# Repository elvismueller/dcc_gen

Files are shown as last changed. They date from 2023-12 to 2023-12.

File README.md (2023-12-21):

dcc_gen
=======

Simple DCC generator for ATMega8 (V2, schematics and board) and ATMega32 (V3-5, only protoypes) to control small isolated layouts.

Features:
- RS232 Interface (9600 baud) for debugging and simple control (use an normal USB to RS232 converter)
- Heartbeat LED should blink roundabout every 2 sek, fast blinking if waiting for second key
- Connect simple switches (ATMega8 10 inputs | ATMega32 4 groups, 20 Inputs, 80 switches in total)
- Support start-end logic and searches for routes in the internal memory
- Setup for USBProg ISP-Interface adapter by www.embeded-projecs.de (for any other modify platformio.ini)

Toolchain (PlatformIo)
- install Visual Studio Code
- install PlatformIO Extension via Extension Manager (left toolbar). Wait til its installed completely (Icon appears in left toolbar)!
- clone, pull and open workspace dcc_gen
- Build it (bottom bar tick icon)Toolchain
- install driver for USBasp with Zadig (https://zadig.akeo.ie/)
  == USBasp (HK version with fischl.de FW): more or less working with: WinUSB v6.1.7600 and libusb_win32, somehow unreliable
  == USBProg 3 running with modified config (check for platformio.ini)
- use "Upload" in Tasks by click on the PlatformIo Icon (Note: returns an error even if the upload was succesful), check avrdude output!

Toolchain Linux (_Archive)
- sudo aptitude install avr-libc avrdude gcc-avr simulavr
- check/use the Makefile

Kown issues: 
- it is NOT a central unit, just a simple generator
- a lot of hardcoded stuff, no SW to init the memory
- bare metal (no Ardunio Code)
- explizit build for either ATMega8 oder ATMega32
- tested only with a few turnout decoder (Claus Illchmann, LDT Datentechnik) some decoder are not working (QDecoder). 
- like almost all motorshields based on this hardware the generatet DCC signal is not recommended for train control. 
- the ATMega8 is very limited in memory and far less verbose (no help etc.)

Helpers
- read fuses with avrdude: .\avrdude -c avrispmkii -p atmega8 -U lfuse:r:-:i -v
- http://www.engbedded.com/fusecalc
- https://hendrich.org/blogs/mikrocontroller/atmega-644-fuses-setzen/
- programm size: C:/Users/EMM/.platformio/packages/toolchain-atmelavr/bin/avr-size --mcu=atmega8 -C .\firmware.elf

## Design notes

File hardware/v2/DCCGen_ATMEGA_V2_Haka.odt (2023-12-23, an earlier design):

# Bauanleitung SimpleSwitcher 2.0

### Kurzbeschreibung

Die Schaltung erzeugt auf Tastendruck Stellbefehle für DCC Magnetartikel. Damit lassen sich kleine Module mit Standard DCC Komponenten ausrüsten und für mobile Anwendung (Modulanlage bei Austellung) mit einem kleinen Stellpult steuern, gleichzeitig aber auch in größere Anlagen integrieren (Automatische Steuerung zuhause)

Herz der Schaltung ist ein Mikrocontroller der ATMEGA Serie von Atmel. Für die PC Anbindung wird die klassische Schaltung mit dem MAX232 verwendet, Endstufe für die Ausgabe des DCC Signals ist ein L298 damit auch etwas Last auf dem Signal möglich ist.

Über eine PC Oberfläche kann jeder Taste mehrere Magnetartikel zugeordnet werden. Dazu ist eine serielle Schnittstelle (USB-RS232-Adapter falls nicht direkt vorhanden) notwendig.

### Schaltplan:

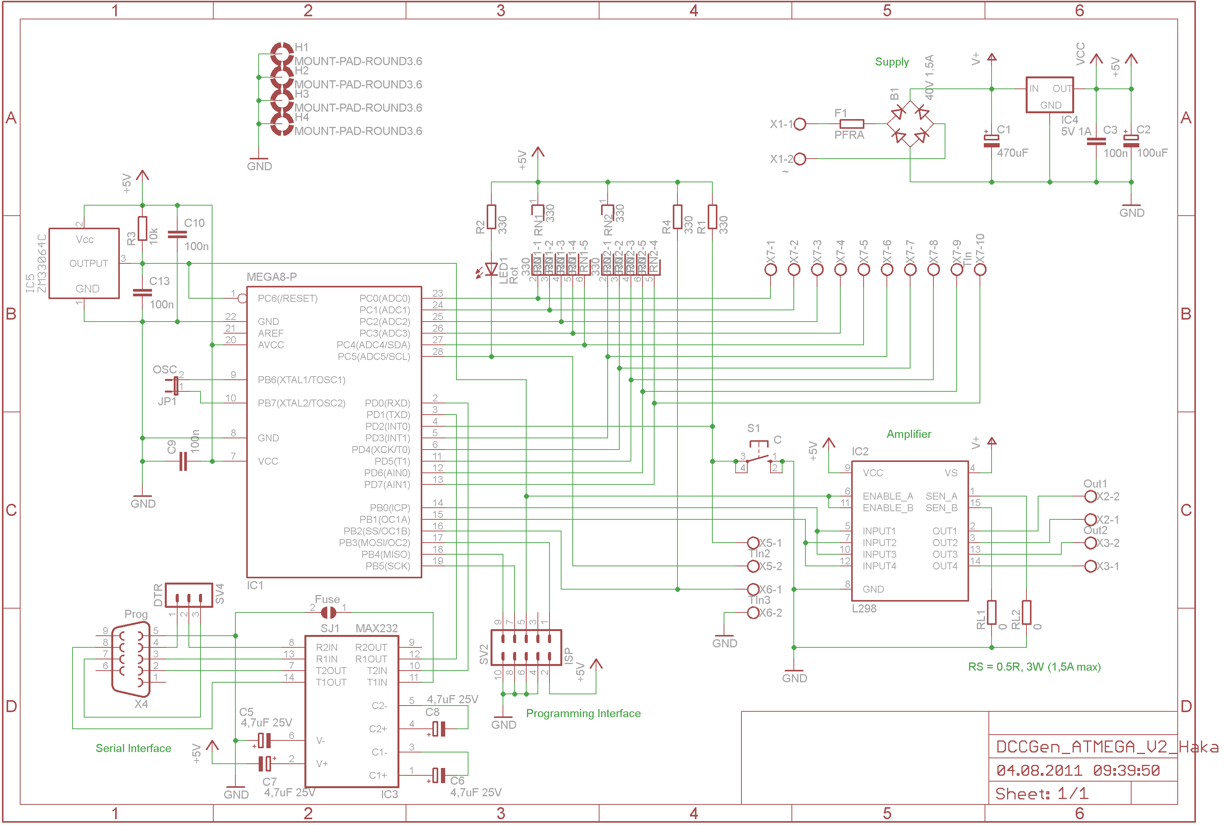
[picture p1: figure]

Beim Aufbau der Schaltung werden die Bauteile der Bauhöhe nach gestaffelt eingebaut. Bei fast allen Bauteilen ist auf die Polung zu achten.

Bei Platinen ohne Bestückungsaufdruck bitte darauf achten das die Bauteile auf die richtige Seite kommen!

Vor dem Einsetzen der IC's das Kapitel Inbetriebnahme lesen!

Viel Glück!

### Bestückungsliste:

Nr. im Plan | Bauteilbeschreibung | Pol? | Reichelt Best.Nr.
R1, R2, R4 | Widerstand 330 Ohm, 1/4W | Nein | 1/4W 330
R3 | Widerstand 10k, 1/4W | Nein | 1/4W 10K
RL1, RL2 | Drahtbrücke | Nein
IC1 | IC-Fassung 28pol | Ja | GS 28-S
IC3 | IC-Fassung 16pol | Ja | GS 16
RN1, RN2 | Widerstandsnetzwerk 6pin, 5x 330 Ohm (andere Werte möglich, nur Pullup) | Ja | SIL 6-5 330
C3, C9, C10, C13 | Keramik Kondensator 100n | Nein | Z5U-2,5 100N
LED1 | LED Rot, 15mA | Ja | LED 3MM RT
IC5 (optional) | Resetcontroller ZM33064C (Ersatz? Ohne?) | Ja | n.a.
B1 | Gleichrichter, 40V, 1.5A | Ja | B40C1500RUND
C5, C6, C7, C8 | Tantal oder Elko, 1uF, min. 25V (siehe Datenblatt!!) | Ja | TANTAL 1,0/35
S1 (optional) | Printtaster, Omron (passt?) | Nein | TASTER 3301
SV2 (optional) | Pfostenleiste, 3pol, einreihig | Nein | SL 1X40G 2,54
SV4 | Pfostenleiste, 10pol, zweireihig | Nein | SL 2X40G 2,54
X1, X2, X3, X5, X6 | Klemmen 2pol | Nein | AKL 057-02
X7 | Klemmen 10pol | Nein | AKL 101-10 oder 5x AKL 057-02
C1 | Elko, 63V, 470uF | Ja | RAD 470/63
C2 | Elko, 35V 100uF | Ja | RAD 10/35
F1 | Halbleitersicherung, 0.5/1A | Nein | PFRA 050
X4 | Sub-D, Print, gewinkelt, 9pol WELCHE??? | Ja | D-SUB BU 09US D-SUB BU 09EU
IC4 | Festspannungsregler 7805 5V, 1A | Ja | µA 7805
IC1 | Mikrocontroller ATMEGA8-P (größere Version??) | Ja | ATMEGA 8-16 DIP (ATMEGA 168-20DIP)
IC2 | L298 | Ja | L 298
IC3 | MAX232 (genauer Typ?) | Ja | MAX 232 CPE

### Korrekturen:

- Am IC MAX232 zusätzlicher Block Kondensator VCC-GND zu Störungsunterdrückung

### Inbetriebnahme

Der Controller arbeitet mit 5V, damit ist die Versorgungsspannung nur durch die gewünschte Digitalspannung definiert. Üblich sind 11-14V~ Wechsel- bzw. 15-20V Gleichspannung. In Verbindung mit Servo-Controller Bausteinen ist es ratsam eher an die untere Grenze zu gehen oder diese komplett separat zu versorgen.

Vor dem Einsetzen der IC's in die Sockel prüfen ob die Versorgungsspannung (Pin 7, Pin 8) am Sockel für den ATMEGA 5V beträgt. Alternativ gemessen über C2.

Dann die IC's einsetzen. Im unprogrammierten Zustand sollte die LED beim Einschalten dreimal blinken und dann erlöschen. Wird ein Eingang betätigt blinkt die LED bis die Fahrstufe abgearbeitet ist.

Zum Testen der Kommunikation mit dem PC die Schaltung an einen freien seriellen Port des PCs anschließen und die Software starten. Die Software sucht automatisch auf allen vorhandenen COM-Ports und verbindet sich mit der Hardware.

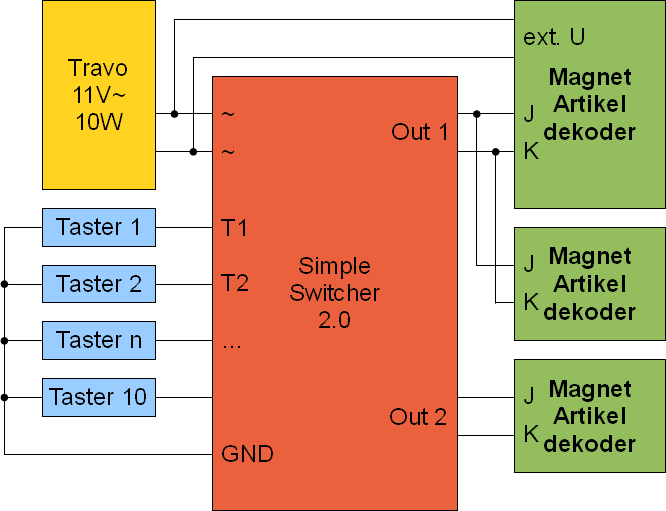
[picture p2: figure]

### Ansicht von der Bestückungsseite

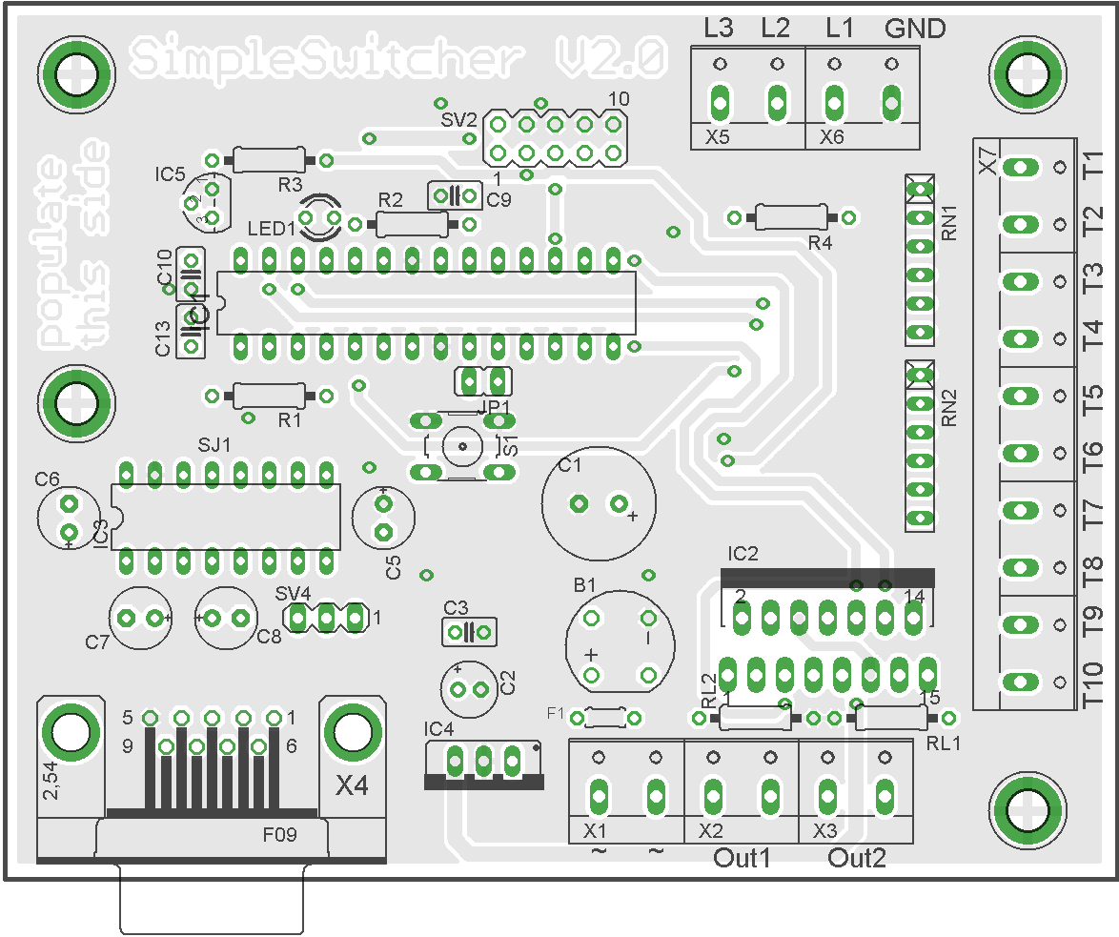
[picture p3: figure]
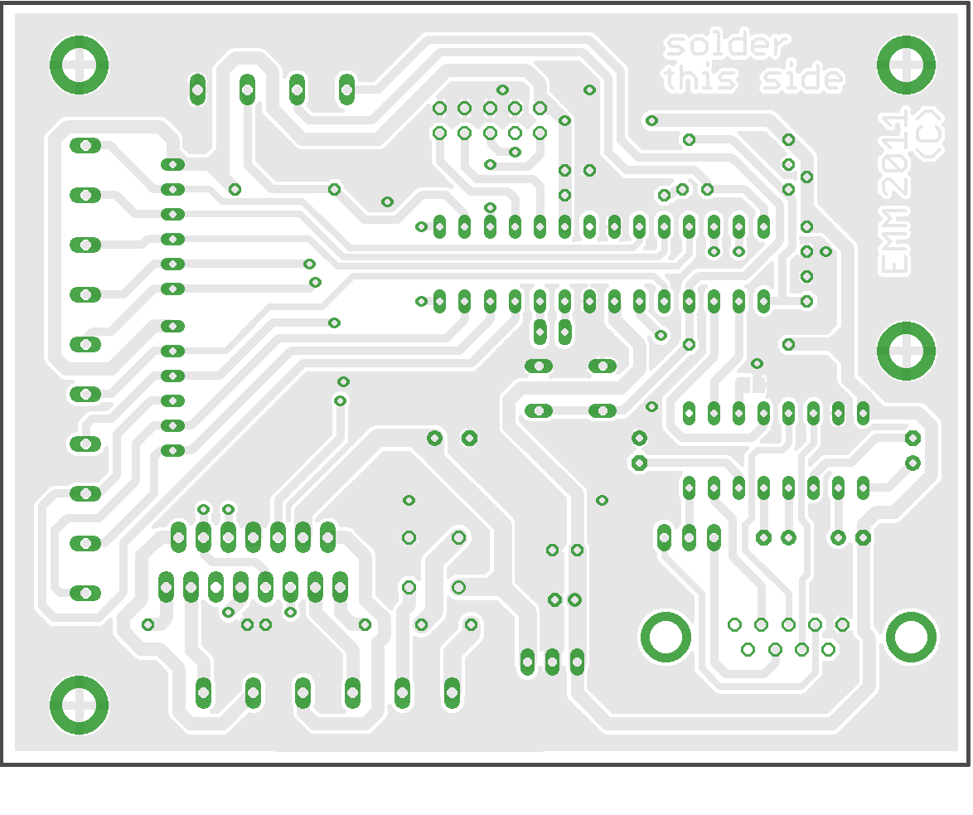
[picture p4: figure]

### Ansicht von der Lötseite

### Kalkulation

Artikel-Nr. | Bezeichnung | WG | Menge | Einzelpreis incl. MwSt. | Gesamtpreis incl. MwSt.
µA 7805 | Spannungsregler 1A positiv, TO-220 | 1 | 1 | 0,29 € | 0,29 €
L 298 | Driver, Multiwatt-15 = L 298N | 1 | 1 | 2,15 € | 2,15 €
ATMEGA 8-16 DIP | ATMega AVR-RISC-Controller, PDIP-28 | 1 | 1 | 2,60 € | 2,60 €
AKL 101-10 | Anschlussklemme 10-polig, RM 5,08 | 1 | 1 | 0,95 € | 0,95 €
AKL 057-02 | Anreihklemme 2-polig, RM5,08 | 1 | 5 | 0,28 € | 1,40 €
1/4W 330 | Kohleschichtwiderstand 1/4W, 5%, 330 Ohm | 1 | 3 | 0,10 € | 0,31 €
1/4W 10K | Kohleschichtwiderstand 1/4W, 5%, 10 K-Ohm | 1 | 1 | 0,10 € | 0,10 €
GS 28-S | IC-Sockel, 28-polig, doppelter Federkontakt | 1 | 1 | 0,080 € | 0,08 €
GS 16 | IC-Sockel, 16-polig, doppelter Federkontakt | 1 | 1 | 0,080 € | 0,08 €
SIL 6-5 330 | Widerstands-Netzwerk, 5Wid./6Pins, 330 Ohm | 1 | 2 | 0,080 € | 0,16 €
Z5U-2,5 100N | Vielschicht-Keramikkondensator 100N, 20% | 1 | 4 | 0,040 € | 0,16 €
LED 3MM RT | LED, 3mm, Low Cost, rot | 1 | 1 | 0,060 € | 0,06 €
B40C1500RUND | RUND-GLEICHRICHTER | 1 | 1 | 0,15 € | 0,15 €
TANTAL 1,0/35 | Tantal-Kondensator, Rm 2,5, 1,0µF/35V | 1 | 4 | 0,14 € | 0,56 €
TASTER 3301 | Kurzhubtaster 6x6mm, Höhe: 4,3mm, 12V, vertikal | 1 | 1 | 0,090 € | 0,09 €
SL 1X40G 2,54 | 40pol. Stiftleiste, gerade, RM 2,54 | 1 | 1 | 0,15 € | 0,15 €
SL 2X40G 2,54 | 2x40pol.-Stiftleiste, gerade, RM 2,54 | 1 | 1 | 0,27 € | 0,27 €
RAD 470/63 | Elektrolytkondensator, 13x25mm, RM 5,0mm | 1 | 1 | 0,14 € | 0,14 €
RAD 10/35 | Elektrolytkondensator, 5x11mm, RM 2,0mm | 1 | 1 | 0,040 € | 0,04 €
PFRA 050 | Rückstellende Sicherungen, max. 40A-60V, 4,0s | 1 | 1 | 0,31 € | 0,31 €
D-SUB BU 09US | D-SUB-Buchse, 9-polig, gewinkelt, RM 7,2 | 1 | 1 | 0,29 € | 0,29 €
MAX 232 CPE | RS232-Driver, DIL-16 | 1 | 1 | 0,41 € | 0,41 €
Warenwert Bauteile | | | | | 10,75 €
Platine | | | | | 20,00 €
Verpackung & Versandkosten | | | | | 5,00 €
Gesamtpreis | | | | | 35,75

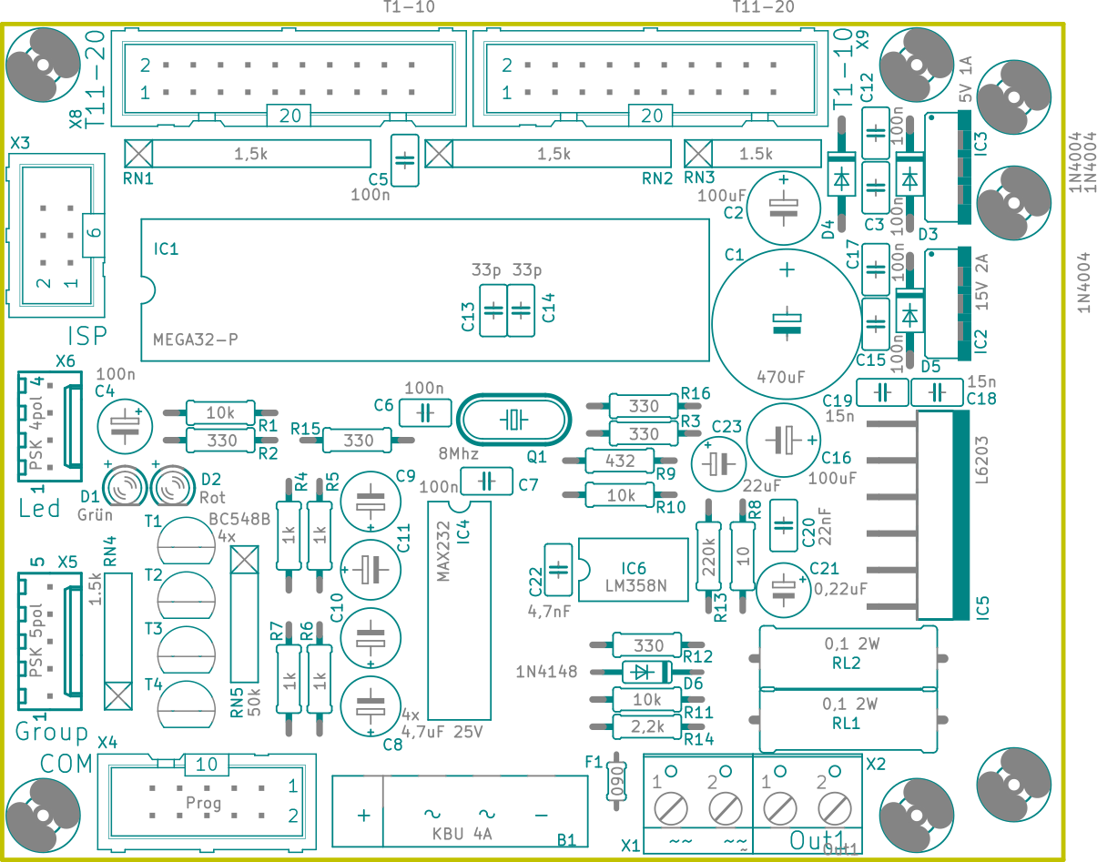
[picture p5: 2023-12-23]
hardware/v5/DCCGen_ATMEGA_V5-brd.png

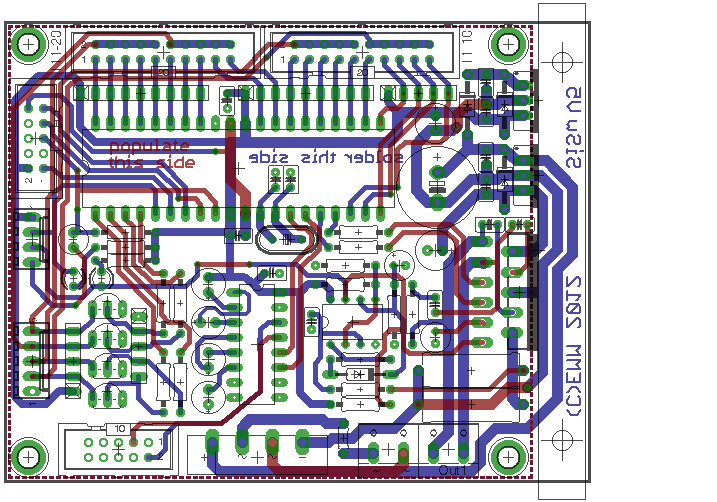
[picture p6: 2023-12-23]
hardware/v5/DCCGen_ATMEGA_V5_Overview.png

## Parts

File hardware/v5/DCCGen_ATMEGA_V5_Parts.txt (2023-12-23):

Partlist

Exported from DCCGen_ATMEGA_V5.sch at 20.07.12 21:43

EAGLE Version 6.2.0 Copyright (c) 1988-2012 CadSoft

Assembly variant: 

Part     Value          Device             Package      Library             Sheet

B1       40V 1.5A       RB1A               RB1A         rectifier           1
C1       470uF          CPOL-EUE5-10.5     E5-10,5      rcl                 1
C2       100uF          CPOL-EUE2-5        E2-5         rcl                 1
C3       100n           C-EU025-025X050    C025-025X050 rcl                 1
C4       100n           CPOL-EUE2.5-5      E2,5-5       rcl                 1
C5       100n           C-EU025-025X050    C025-025X050 rcl                 1
C6       100n           C-EU025-025X050    C025-025X050 rcl                 1
C7       100n           C-EU025-025X050    C025-025X050 rcl                 1
C8       4,7uF 25V      CPOL-EUE2,5-6E     E2,5-6E      rcl                 1
C9       4,7uF 25V      CPOL-EUE2,5-6E     E2,5-6E      rcl                 1
C10      4,7uF 25V      CPOL-EUE2,5-6E     E2,5-6E      rcl                 1
C11      4,7uF 25V      CPOL-EUE2,5-6E     E2,5-6E      rcl                 1
C12      100n           C-EU025-025X050    C025-025X050 rcl                 1
C13      33p            C-EU025-025X050    C025-025X050 rcl                 1
C14      33p            C-EU025-025X050    C025-025X050 rcl                 1
C15      100n           C-EU025-025X050    C025-025X050 rcl                 1
C16      100uF          CPOL-EUE2-5        E2-5         rcl                 1
C17      100n           C-EU025-025X050    C025-025X050 rcl                 1
C18      15n            C-EU025-025X050    C025-025X050 rcl                 1
C19      15n            C-EU025-025X050    C025-025X050 rcl                 1
C20      22nF           C-EU025-025X050    C025-025X050 rcl                 1
C21      0,22uF         CPOL-EUE2-5        E2-5         rcl                 1
C22      4,7nF          C-EU025-025X050    C025-025X050 rcl                 1
C23      22uF           CPOL-EUE2-5        E2-5         rcl                 1
D1       Rot            LED3MM             LED3MM       led                 1
D2       1N4004         1N4004             DO41-10      diode               1
D3       1N4004         1N4004             DO41-10      diode               1
D4       1N4004         1N4004             DO41-10      diode               1
D5       1N4148         1N4148DO35-10      DO35-10      diode               1
D6       Rot            LED3MM             LED3MM       led                 1
F1       PFRA           R-EU_0204/5        0204/5       rcl                 1
H1       3.6            MOUNT-PAD-ROUND3.6 3,6-PAD      holes               1
H2       3.6            MOUNT-PAD-ROUND3.6 3,6-PAD      holes               1
H3       3.6            MOUNT-PAD-ROUND3.6 3,6-PAD      holes               1
H4       3.6            MOUNT-PAD-ROUND3.6 3,6-PAD      holes               1
IC1      MEGA32-P       MEGA32-P           DIL40        atmel               1
IC2      15V 2A         78XXS              78XXS        v-reg               1
IC3      MAX232         MAX232             DIL16        maxim               1
IC4      5V 1A          78XXS              78XXS        v-reg               1
IC5      L6203          L6203              MULTIWATT-11 st-microelectronics 1
IC6      LM358N         LM358N             DIL08        linear              1
Q1       8Mhz           CRYSTALHC49U-V     HC49U-V      crystal             1
R1       10k            R-EU_0207/10       0207/10      rcl                 1
R2       330            R-EU_0207/10       0207/10      rcl                 1
R3       330            R-EU_0207/10       0207/10      rcl                 1
R4       1k             R-EU_0207/10       0207/10      rcl                 1
R5       1k             R-EU_0207/10       0207/10      rcl                 1
R6       1k             R-EU_0207/10       0207/10      rcl                 1
R7       1k             R-EU_0207/10       0207/10      rcl                 1
R8       10             R-EU_0207/10       0207/10      rcl                 1
R9       432            R-EU_0207/10       0207/10      rcl                 1
R10      10k            R-EU_0207/10       0207/10      rcl                 1
R11      10k            R-EU_0207/10       0207/10      rcl                 1
R12      330            R-EU_0207/10       0207/10      rcl                 1
R13      220k           R-EU_0207/10       0207/10      rcl                 1
R16      2,2k           R-EU_0207/10       0207/10      rcl                 1
R17      330            R-EU_0207/10       0207/10      rcl                 1
RL1      0,1 2W         R-EU_0411/15       0411/15      rcl                 1
RL2      0,1 2W         R-EU_0411/15       0411/15      rcl                 1
RN1      1,5k           RNX8               RN-9         resistor-net        1
RN2      1,5k           RNX8               RN-9         resistor-net        1
RN3      1.5k           RNX4               RN-5         resistor-net        1
RN4      1.5k           RNX4               RN-5         resistor-net        1
RN5      50k            RNX4               RN-5         resistor-net        1
SJ1      Fuse           SJ                 SJ           jumper              1
SJ2      Fuse           SJ                 SJ           jumper              1
SJ7      0              SJ                 SJ           jumper              1
T1       BC548B         BC548B             TO92-EBC     transistor-npn      1
T2       BC548B         BC548B             TO92-EBC     transistor-npn      1
T3       BC548B         BC548B             TO92-EBC     transistor-npn      1
T4       BC548B         BC548B             TO92-EBC     transistor-npn      1
X1       ~              W237-02P           W237-132     con-wago-508        1
X2       Out1           W237-02P           W237-132     con-wago-508        1
X4       Prog           F09VP              F09VP        con-subd            1
X5       group          W237-05P           W237-5P      con-wago-508        1
X6       ISP            ML10               ML10         con-ml              1
X7       led            W237-02P           W237-132     con-wago-508        1
X8       T1-10          ML20               ML20         con-ml              1
X9       T11-20         ML20               ML20         con-ml              1

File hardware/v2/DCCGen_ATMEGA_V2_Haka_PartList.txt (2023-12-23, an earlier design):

Partlist

Exported from DCCGen_ATMEGA_V2_Haka.sch at 05.08.2011 10:19:21

EAGLE Version 5.11.0 Copyright (c) 1988-2010 CadSoft

Part     Value              Device             Package      Library             Sheet

B1       40V 1.5A           RB1A               RB1A         rectifier           1
C1       470uF              CPOL-EUE3.5-10     E3,5-10      rcl                 1
C2       100uF              CPOL-EUE2-5        E2-5         rcl                 1
C3       100n               C-EU025-025X050    C025-025X050 rcl                 1
C5       4,7uF 25V          CPOL-EUE2,5-6E     E2,5-6E      rcl                 1
C6       4,7uF 25V          CPOL-EUE2,5-6E     E2,5-6E      rcl                 1
C7       4,7uF 25V          CPOL-EUE2,5-6E     E2,5-6E      rcl                 1
C8       4,7uF 25V          CPOL-EUE2,5-6E     E2,5-6E      rcl                 1
C9       100n               C-EU025-025X050    C025-025X050 rcl                 1
C10      100n               C-EU025-025X050    C025-025X050 rcl                 1
C13      100n               C-EU025-025X050    C025-025X050 rcl                 1
F1       PFRA               R-EU_0204/5        0204/5       rcl                 1
H1       MOUNT-PAD-ROUND3.6 MOUNT-PAD-ROUND3.6 3,6-PAD      holes               1
H2       MOUNT-PAD-ROUND3.6 MOUNT-PAD-ROUND3.6 3,6-PAD      holes               1
H3       MOUNT-PAD-ROUND3.6 MOUNT-PAD-ROUND3.6 3,6-PAD      holes               1
H4       MOUNT-PAD-ROUND3.6 MOUNT-PAD-ROUND3.6 3,6-PAD      holes               1
IC1      MEGA8-P            MEGA8-P            DIL28-3      atmel               1
IC2      L298               L298               MULTIWATT-15 st-microelectronics 1
IC3      MAX232             MAX232             DIL16        maxim               1
IC4      5V 1A              78XXS              78XXS        v-reg               1
IC5      ZM33064C           ZM33064C           TO92         andereBauteile      1
JP1      OSC                JP1E               JP1          jumper              1
LED1     Rot                LED3MM             LED3MM       led                 1
R1       330                R-EU_0207/10       0207/10      rcl                 1
R2       330                R-EU_0207/10       0207/10      rcl                 1
R3       10k                R-EU_0207/10       0207/10      rcl                 1
R4       330                R-EU_0207/10       0207/10      rcl                 1
RL1      0                  R-EU_0207/10       0207/10      rcl                 1
RL2      0                  R-EU_0207/10       0207/10      rcl                 1
RN1      330                RNX5               RN-6         resistor-net        1
RN2      330                RNX5               RN-6         resistor-net        1
S1       C                  10-XX              B3F-10XX     switch-omron        1
SJ1      Fuse               SJ                 SJ           jumper              1
SV2      ISP                MA05-2             MA05-2       con-lstb            1
SV4      DTR                MA03-1             MA03-1       con-lstb            1
X1       ~                  W237-02P           W237-132     con-wago-508        1
X2       Out1               W237-02P           W237-132     con-wago-508        1
X3       Out2               W237-02P           W237-132     con-wago-508        1
X4       Prog               F09HP              F09HP        con-subd            1
X5       TIn2               W237-02P           W237-132     con-wago-508        1
X6       TIn3               W237-02P           W237-132     con-wago-508        1
X7       TIn                W237-10P           W237-10P     con-wago-508        1

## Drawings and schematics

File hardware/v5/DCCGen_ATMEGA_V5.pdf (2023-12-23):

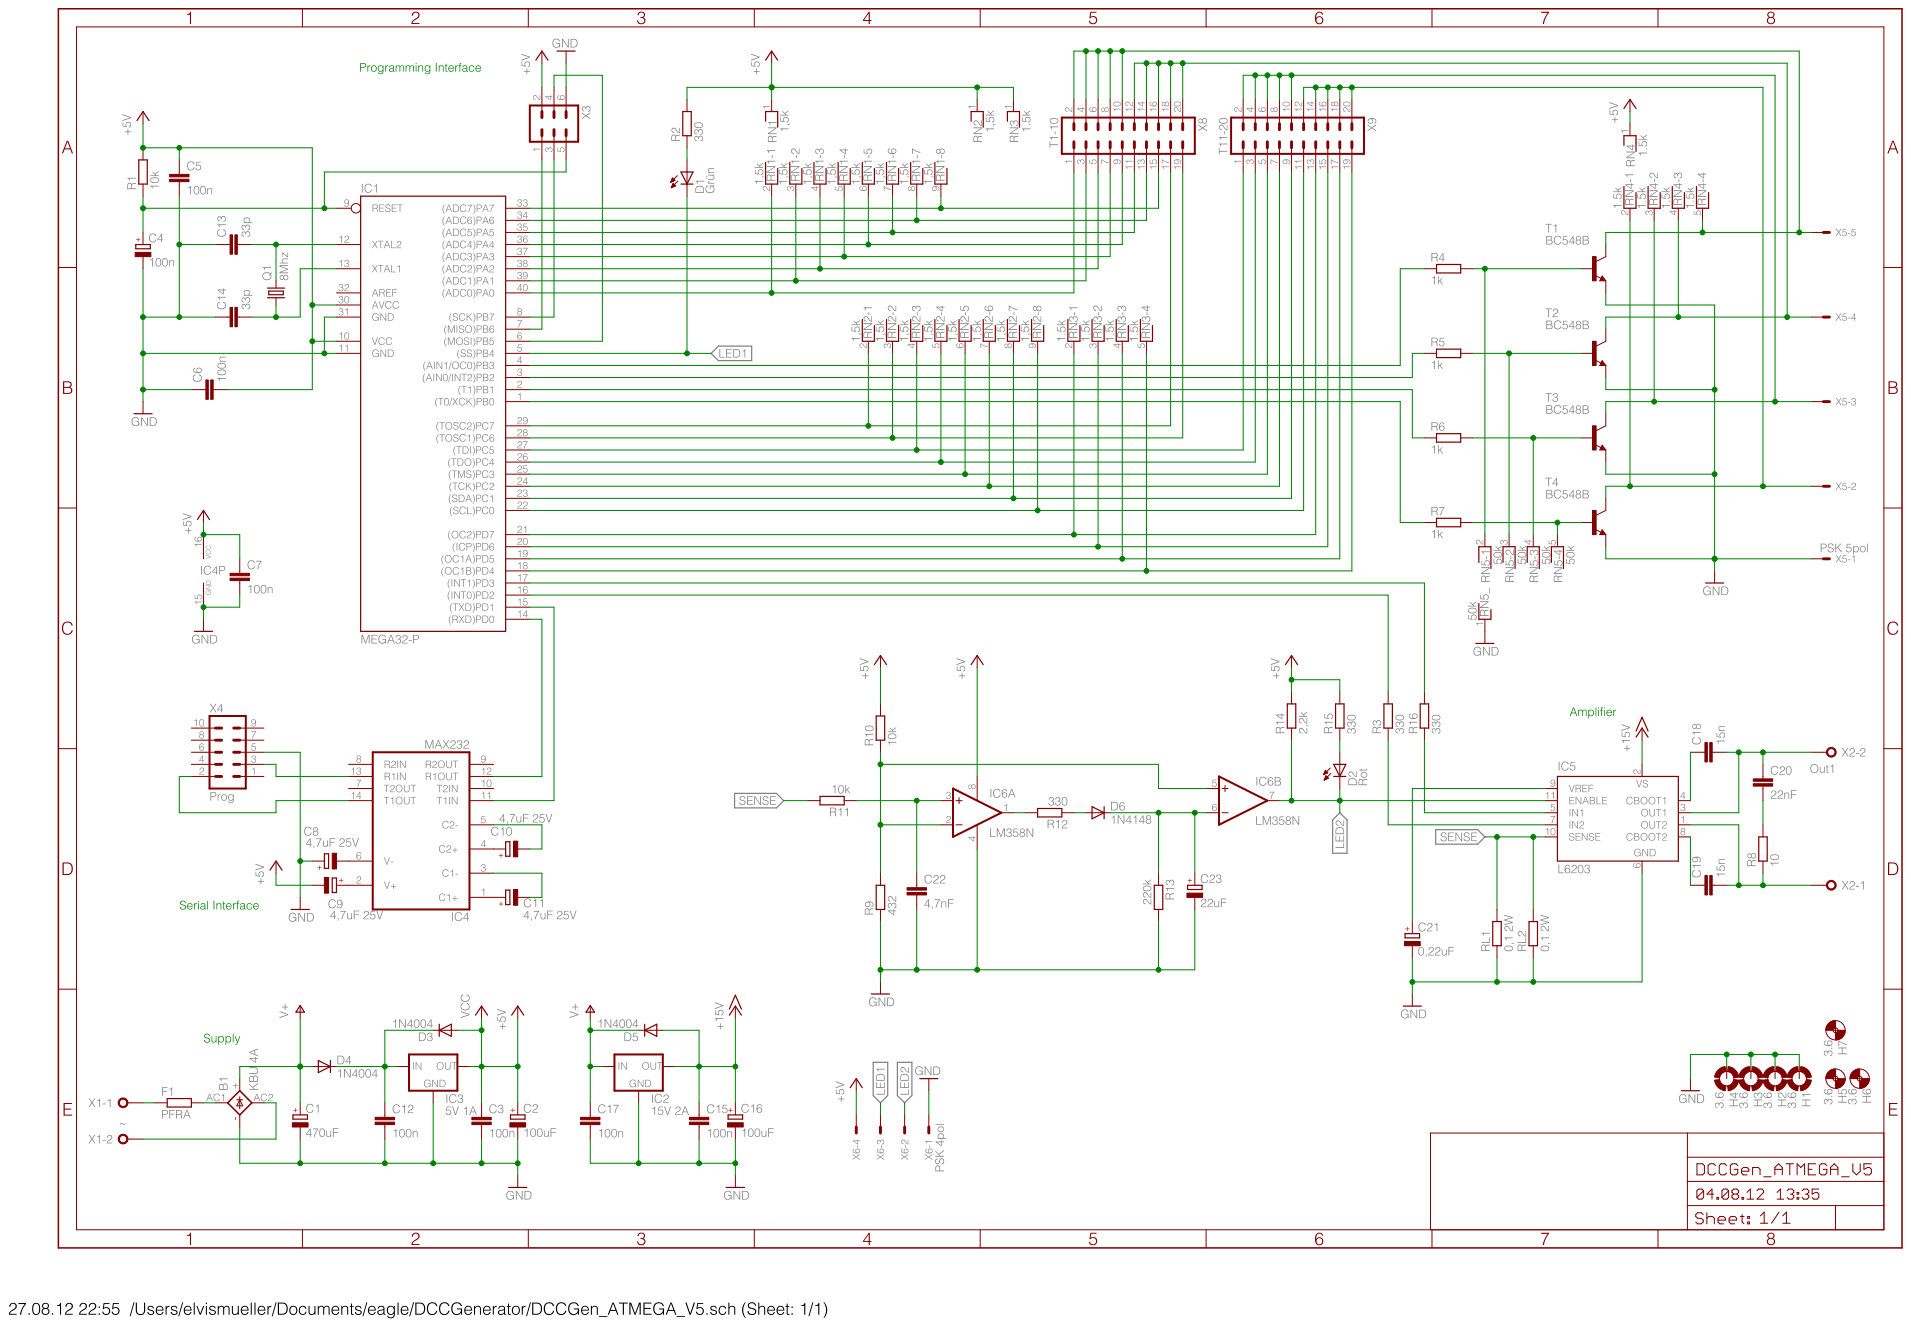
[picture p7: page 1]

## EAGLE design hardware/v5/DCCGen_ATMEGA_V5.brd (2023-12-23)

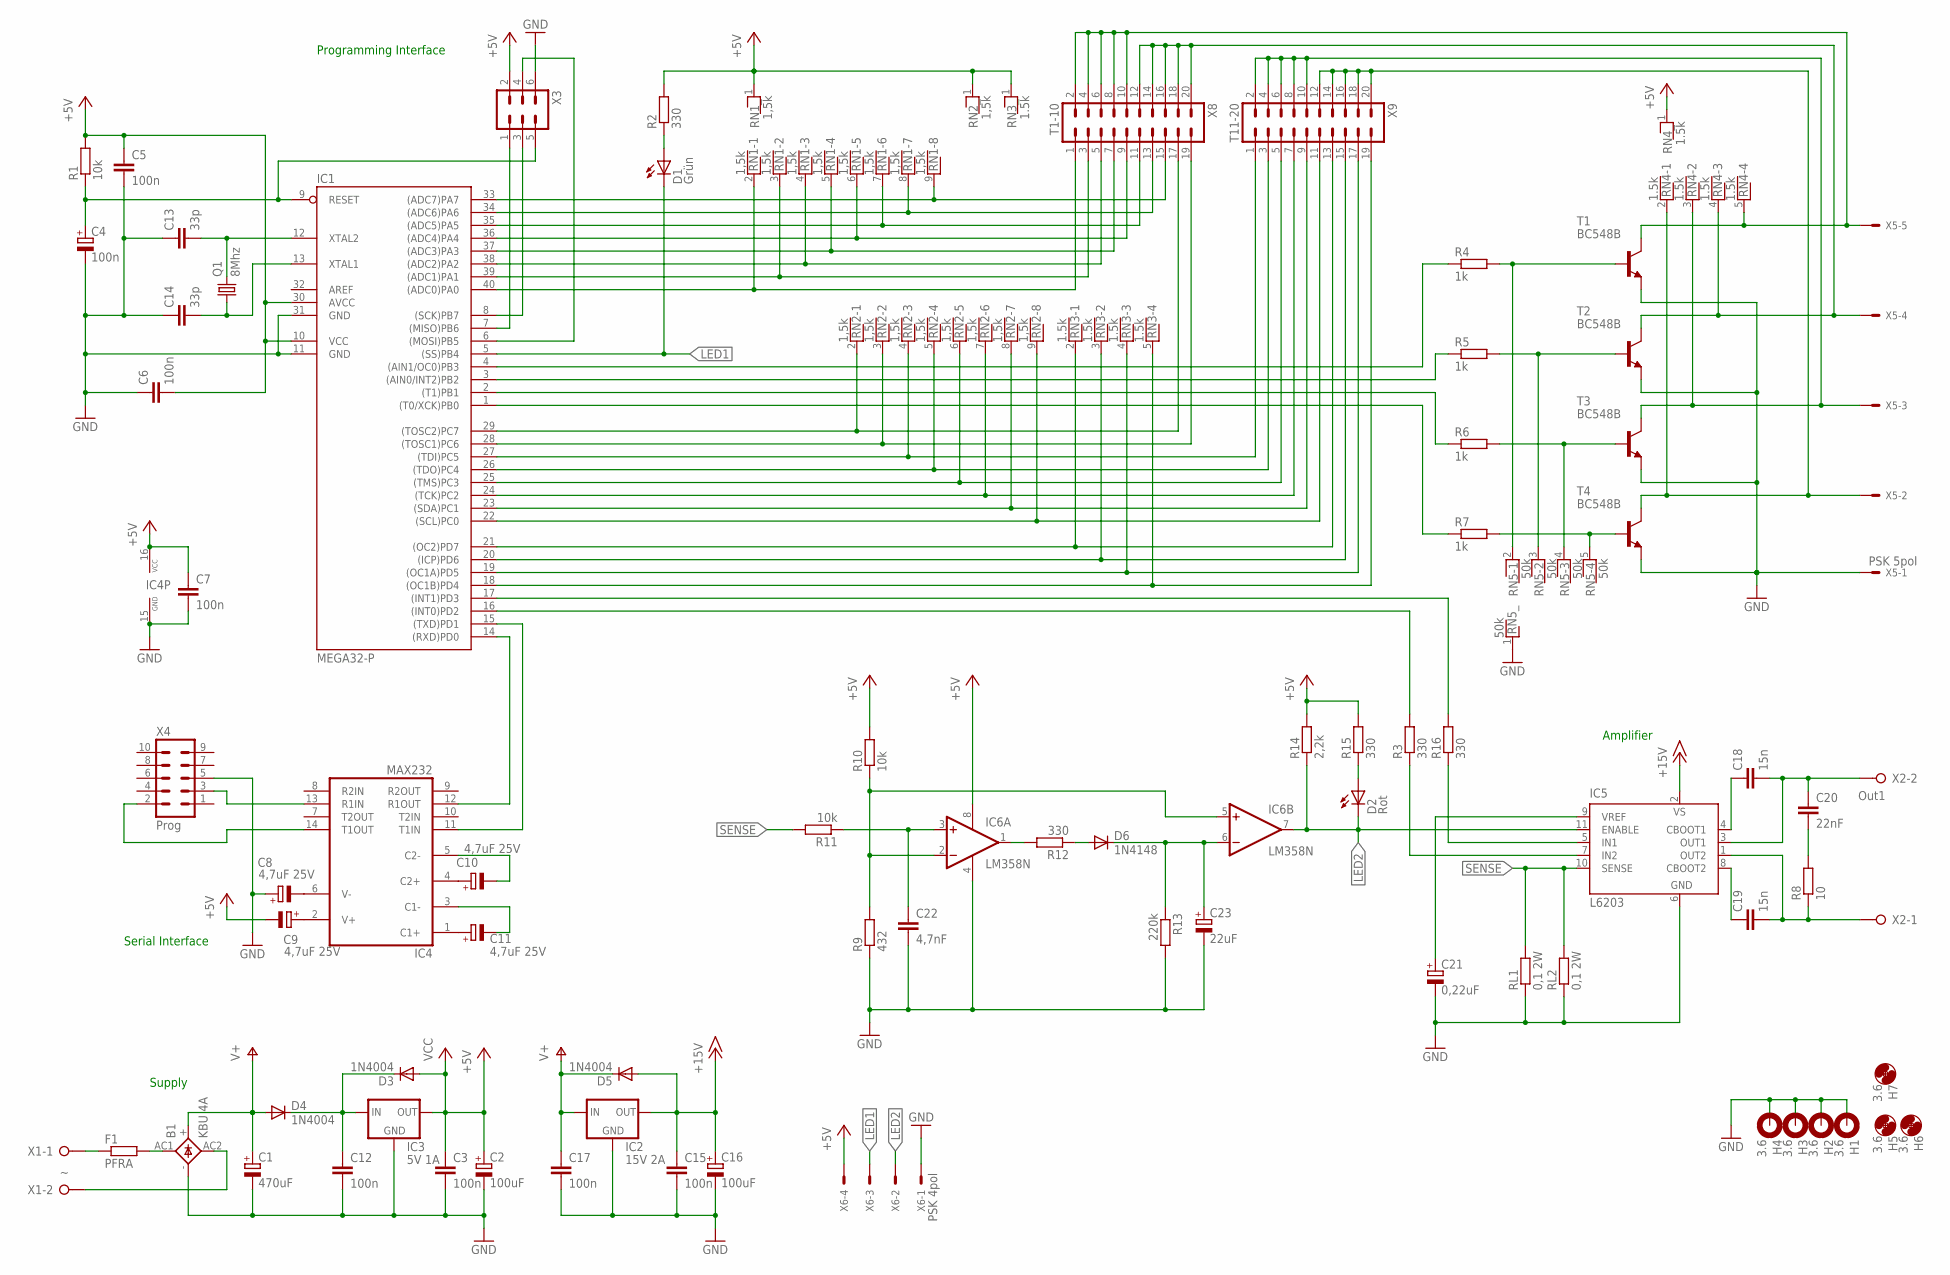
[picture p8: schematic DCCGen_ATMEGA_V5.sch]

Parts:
B1: KBU 4A; KBU
C1: 470uF; E5-13
C2, C16: 100uF; E2,5-7
C3, C5, C6, C7, C12, C15, C17: 100n; C025-025X050
C4: 100n; E2,5-5
C8, C9, C10, C11: 4,7uF 25V; E2,5-6E
C13, C14: 33p; C025-025X050
C18, C19: 15n; C025-025X050
C20: 22nF; C025-025X050
C21: 0,22uF; E2-5
C22: 4,7nF; C025-025X050
C23: 22uF; E2-5
D1: Grün; LED3MM
D2: Rot; LED3MM
D3, D4, D5: 1N4004; DO41-10
D6: 1N4148; DO35-10
F1: PFRA; 0204/5
H1, H2, H3, H4: 3.6; 3,6-PAD
H5, H6, H7: 3.6; 3,6
IC1: MEGA32-P; DIL40
IC2: 15V 2A; 78XXS
IC3: 5V 1A; 78XXS
IC4: MAX232; DIL16
IC5: L6203; MULTIWATT-11
IC6: LM358N; DIL08
Q1: 8Mhz; HC49U-V
R1, R10, R11: 10k; 0207/10
R2, R3, R12, R15, R16: 330; 0207/10
R4, R5, R6, R7: 1k; 0207/10
R8: 10; 0207/10
R9: 432; 0207/10
R13: 220k; 0207/10
R14: 2,2k; 0207/10
RL1, RL2: 0,1 2W; 0617/17
RN1, RN2: 1,5k; RN-9
RN3, RN4: 1.5k; RN-5
RN5: 50k; RN-5
T1, T2, T3, T4: BC548B; TO92-EBC
X1: W237-132
X2: Out1; W237-132
X3: ML6
X4: Prog; ML10
X5: PSK 5pol; 6410-05
X6: PSK 4pol; 6410-04
X8: T1-10; ML20
X9: T11-20; ML20

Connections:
+5V: C2.+, C3.1, C5.1, C6.2, C7.1, C9.-, D3.A, IC1.10 (VCC), IC1.30 (AVCC), IC3.OUT, IC4.16 (VCC), IC6.8 (V+), R1.2, R2.2, R10.2, R14.2, R15.2, RN1.1, RN2.1, RN3.1, RN4.1, X3.2, X6.4
+15V: C15.1, C16.+, D5.A, IC2.OUT, IC5.2 (VS)
GND: B1.-, C1.-, C2.-, C3.2, C4.-, C5.2, C6.1, C7.2, C8.+, C12.2, C13.1, C14.1, C15.2, C16.-, C17.2, C21.-, C22.2, C23.-, H1.B3,6, H2.B3,6, H3.B3,6, H4.B3,6, IC1.11 (GND), IC1.31 (GND), IC2.GND, IC3.GND, IC4.15 (GND), IC5.6 (GND), IC6.4 (V-), R9.1, R13.2, RL1.1, RL2.1, RN5.1, T1.E, T2.E, T3.E, T4.E, X3.6, X4.5, X5.1, X6.1
LED1: D1.K (C), IC1.5 ((SS)PB4), X6.3
LED2: D2.K (C), IC5.11 (ENABLE), IC6.7 (OUT), R14.1, X6.2
unnamed: F1.1, X1.1
unnamed: B1.AC2, X1.2
unnamed: IC1.6 ((MOSI)PB5), X3.4
unnamed: IC1.8 ((SCK)PB7), X3.3
unnamed: IC1.7 ((MISO)PB6), X3.1
unnamed: IC1.40 ((ADC0)PA0), RN1.2, X8.1
unnamed: IC1.39 ((ADC1)PA1), RN1.3, X8.3
unnamed: IC1.38 ((ADC2)PA2), RN1.4, X8.5
unnamed: C4.+, IC1.9 (RESET), R1.1, X3.5
unnamed: IC1.37 ((ADC3)PA3), RN1.5, X8.7
unnamed: IC1.36 ((ADC4)PA4), RN1.6, X8.9
unnamed: IC1.35 ((ADC5)PA5), RN1.7, X8.11
unnamed: IC1.34 ((ADC6)PA6), RN1.8, X8.13
unnamed: IC1.33 ((ADC7)PA7), RN1.9, X8.15
unnamed: C14.2, IC1.13 (XTAL1), Q1.1
unnamed: C12.1, D3.C, D4.C, IC3.IN
unnamed: D1.A, R2.1
unnamed: IC1.29 ((TOSC2)PC7), RN2.2, X8.17
unnamed: IC1.28 ((TOSC1)PC6), RN2.3, X8.19
unnamed: IC1.27 ((TDI)PC5), RN2.4, X9.1
unnamed: C21.+, IC5.9 (VREF)
unnamed: IC1.26 ((TDO)PC4), RN2.5, X9.3
unnamed: IC6.2 (-IN), IC6.5 (+IN), R9.2, R10.1
unnamed: C22.1, IC6.3 (+IN), R11.1
unnamed: C20.2, R8.2
unnamed: IC1.17 ((INT1)PD3), R16.2
unnamed: IC1.16 ((INT0)PD2), R3.2
unnamed: C18.2, C20.1, IC5.3 (OUT1), X2.2
unnamed: C18.1, IC5.4 (CBOOT1)
unnamed: IC1.15 ((TXD)PD1), IC4.11 (T1IN)
unnamed: IC1.14 ((RXD)PD0), IC4.12 (R1OUT)
unnamed: C8.-, IC4.6 (V-)
unnamed: C9.+, IC4.2 (V+)
unnamed: IC4.14 (T1OUT), X4.2
unnamed: C11.+, IC4.1 (C1+)
unnamed: C11.-, IC4.3 (C1-)
unnamed: C10.+, IC4.4 (C2+)
unnamed: C10.-, IC4.5 (C2-)
unnamed: IC4.13 (R1IN), X4.3
unnamed: IC1.25 ((TMS)PC3), RN2.6, X9.5
unnamed: B1.AC1, F1.2
unnamed: IC1.24 ((TCK)PC2), RN2.7, X9.7
unnamed: IC1.23 ((SDA)PC1), RN2.8, X9.9
unnamed: IC1.22 ((SCL)PC0), RN2.9, X9.11
unnamed: IC1.21 ((OC2)PD7), RN3.2, X9.13
unnamed: IC1.20 ((ICP)PD6), RN3.3, X9.15
unnamed: IC1.19 ((OC1A)PD5), RN3.4, X9.17
unnamed: IC1.18 ((OC1B)PD4), RN3.5, X9.19
unnamed: IC5.7 (IN2), R3.1
unnamed: IC5.5 (IN1), R16.1
unnamed: RN4.2, T4.C, X5.2, X9.12, X9.14, X9.16, X9.18, X9.20
unnamed: IC1.2 ((T1)PB1), R6.1
unnamed: IC1.1 ((T0/XCK)PB0), R7.1
unnamed: IC1.4 ((AIN1/OC0)PB3), R4.1
unnamed: IC1.3 ((AIN0/INT2)PB2), R5.1
unnamed: R4.2, RN5.2, T1.B
unnamed: R5.2, RN5.3, T2.B
unnamed: R6.2, RN5.4, T3.B
unnamed: R7.2, RN5.5, T4.B
unnamed: C13.2, IC1.12 (XTAL2), Q1.2
unnamed: C19.1, IC5.8 (CBOOT2)
unnamed: C19.2, IC5.1 (OUT2), R8.1, X2.1
unnamed: IC6.1 (OUT), R12.2
unnamed: C23.+, D6.C, IC6.6 (-IN), R13.1
unnamed: D6.A, R12.1
unnamed: RN4.5, T1.C, X5.5, X8.2, X8.4, X8.6, X8.8, X8.10
unnamed: RN4.4, T2.C, X5.4, X8.12, X8.14, X8.16, X8.18, X8.20
unnamed: RN4.3, T3.C, X5.3, X9.2, X9.4, X9.6, X9.8, X9.10
unnamed: D2.A, R15.1
SENSE: IC5.10 (SENSE), R11.2, RL1.2, RL2.2
V+: B1.+, C1.+, C17.1, D4.A, D5.C, IC2.IN

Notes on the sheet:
Serial Interface
Programming Interface
Amplifier
Supply

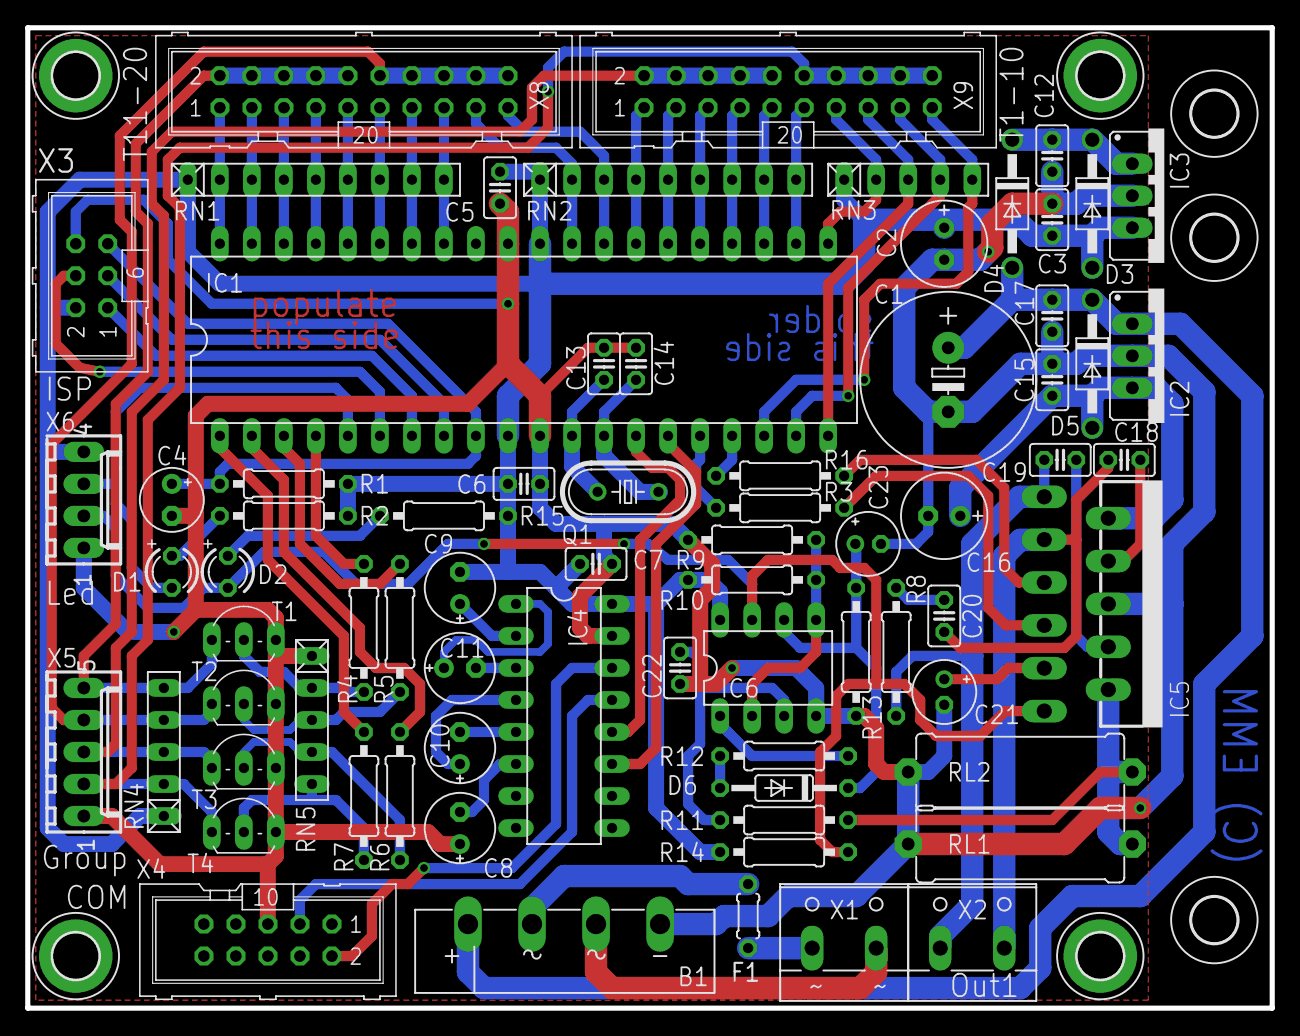
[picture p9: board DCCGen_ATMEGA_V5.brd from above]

Board: 2 copper layers, 98.7 x 77.8 mm, 80 parts (0 on the bottom side), 76 nets.

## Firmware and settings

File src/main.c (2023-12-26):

/*
 *******************************************************************************************
 dcc_gen V3.0
 - new uC: ATMEGA32
 - Start-Target Feature
 - improved Console Functions
 dcc_gen V3.1
 - (2022-4-15) SETUP: fix programmer config (platformio.ini), runs now with USBProg3.0 again
               ATMEGA8: reduce RAM: less Routes, no selftest, Known Issue: still problems with UART
               DCC: changed sync length to 16 iterations, use utils/delay functions,
                    re-adjust DCC bit length, fix switch command (add active flag)
               GENERAL: cleanup unused functions, remove white spaces, formating, renaming
 - (2022-4-28) SETUP: fix programmer config for USBasp (FW 2011)
               ATMEGA8: refactor state machine, fixed memory issue (also fixes the UART)
 - (2023-12-21 add parameter to switch off idle toggle, add toggle for switches, fix delays, optimize flash
 *******************************************************************************************
*/
#define VERSION 3
#define SUBVERSION 1
#ifdef __AVR_ATmega32__
  #define MEGA_CPU 32
#endif
#ifdef __AVR_ATmega8__
  #define MEGA_CPU 8
#endif

#ifdef __AVR_ATmega32__
 #define PIN_OUT1 PD2
 #define PIN_OUT2 PD3
#endif

#include "avr/io.h"
#include <avr/interrupt.h>
#include <string.h>
#include <stdio.h>
#include <stdlib.h>
#include "avr/eeprom.h"
#include <avr/pgmspace.h>
#include <util/delay.h>

#define false 0
#define true 1
  
//******************************************************************************************
// Berechnung des Wertes fuer das Baudratenregister
// aus Taktrate und gewuenschter Baudrate
//******************************************************************************************
#ifndef F_CPU
/* In neueren Version der WinAVR/Mfile Makefile-Vorlage kann
   F_CPU im Makefile definiert werden, eine nochmalige Definition
   hier wuerde zu einer Compilerwarnung fuehren. Daher "Schutz" durch
   #ifndef/#endif

   Dieser "Schutz" kann zu Debugsessions fuehren, wenn AVRStudio
   verwendet wird und dort eine andere, nicht zur Hardware passende
   Taktrate eingestellt ist: Dann wird die folgende Definition
   nicht verwendet, sondern stattdessen der Defaultwert (8 MHz?)
   von AVRStudio - daher Ausgabe einer Warnung falls F_CPU
   noch nicht definiert: */
#warning "F_CPU war noch nicht definiert, wird nun nachgeholt mit 8000000"
#define F_CPU 8000000UL  // Systemtakt in Hz - Definition als unsigned long beachten
                         // Ohne ergeben sich unten Fehler in der Berechnung
#endif
#define BAUD 9600UL      // Baudrate
// Berechnungen
#define UBRR_VAL ((F_CPU+BAUD*8)/(BAUD*16)-1)   // clever runden
#define BAUD_REAL (F_CPU/(16*(UBRR_VAL+1)))     // Reale Baudrate
#define BAUD_ERROR ((BAUD_REAL*1000)/BAUD)      // Fehler in Promille, 1000 = kein Fehler.
#if ((BAUD_ERROR<990) || (BAUD_ERROR>1010))
  #error Systematischer Fehler der Baudrate groesser 1% und damit zu hoch!
#endif
// Quelle: www.mikrocontroller.net AVR GCC Tutorial
//******************************************************************************************

//******************************************************************************************
// function prototypes
//******************************************************************************************
void InitPorts(void);
void InitTimer(void);
void HeartbeatSet(unsigned char state);
void Selftest(void);
int main(void);

//DCC functions
void DCCSet(void);
void DCCDelete(void);
void DCCBitOne(void);
void DCCBitZero(void);
void DCCBitZeroLong(void);
void DCCSync(void);
void DCCStartbit(void);
void DCCByte(char cByte);
void DCCStopbit(void);
char DCCSwitch
       ( unsigned char p_cDecAdresse
       , unsigned char p_cDecOutput
       , unsigned char p_cState
       );
void DCCToggle(void);

//delay functions
void delay_ms(unsigned int uiDuration);
void delay_us(unsigned int uiDuration);

//UART functions
void UARTInit(void);
char UARTReceive(void);
char UARTGetC(void);
void UARTTransmit(char data);
void UARTSendString(const char * pStr);
void UARTHello(void);
void UARTCheckCommand(void);
void UARTSendHelp(void); 
void UARTComunicate(void);
void UARTSendMemoryElements(void);
void UARTSendMemoryRoutes(void);
char UARTSendMemoryTrace(unsigned char route);
void UARTSendMemoryOverview(void);
char UARTToggleSwitches(unsigned char fromSwitch, unsigned char toSwitch);

//define stream for printf
static FILE uart_stream = FDEV_SETUP_STREAM((void *)UARTTransmit,NULL, _FDEV_SETUP_RW);

//protocol functions
char GetTokenToChar
       ( char * pcBuffer
       , char cIndex
       );
unsigned char GetTokenToUChar
       ( char * pcBuffer
       , char cIndex
       );

void CopyNumericToken
       ( char * dest
       , char * src
       , char length
       );

//keyboard functions
void KeybRead(void);
char KeybIsKey(unsigned char Index);

//memory functions
char MemoryReadFromEEprom(void);
char MemorySaveToEEprom(void);
void MemoryInit(void);
char MemorySetElement
       ( unsigned char index
       , unsigned char assigned_id
       , unsigned char dec_adr
       , unsigned char dec_state
       );
char MemorySetElementWait
       ( unsigned char index
       , unsigned char assigned_id
       , unsigned char dec_adr
       , unsigned char dec_state
       , unsigned char wait
       , unsigned char forward
       );
char MemorySetRoute
       ( unsigned char index
       , unsigned char fromKey
       , unsigned char toKey
       , unsigned char bidirectional
       , unsigned char targetDefined
       );
void MemoryTestInit(char token);
void MemoryClear(void);
void MemorySwitchField
       ( unsigned char line
       , unsigned char field
       );
char MemoryCareTargetlessRoutes
       ( unsigned char FirstPressedKey
       );
void MemoryCareCompleteRoutes
       ( unsigned char FirstPressedKey
       , unsigned char SecondPressedKey
       );

//task functions
void LEDTask(void);
void MemoryTask(void);
void KeybTask(void);

//******************************************************************************************
// data and structures memory
//******************************************************************************************
#define MAX_DECODER_ADRESS                        128
#define MAX_BIDIRECTIONAL                         1
#define MAX_DECODER_STATE                         1
#define MAX_KEYS_COUNT_LIMIT                      10
#define MAX_DECODER_WAIT                          16
#define MAX_DECODER_FORWARD_ROUTE                 1


#ifdef __AVR_ATmega8__
  #define MAX_MEMORY_ELEMENTS                     0x8F
  #define MAX_MEMORY_ROUTES                       60
  #define MAX_KEY_GROUPS                          1
  #define MAX_REAL_KEYS                           10
#endif

#ifdef __AVR_ATmega32__
  #define MAX_MEMORY_ELEMENTS                     240
  #define MAX_MEMORY_ROUTES                       120
  #define MAX_KEY_GROUPS                          4
  #define MAX_REAL_KEYS                           20
#endif

#define MAX_VIRTUAL_KEYS                          (MAX_REAL_KEYS * MAX_KEY_GROUPS)

struct MemoryElement 
{ unsigned char assigned_id;//assigned route
  unsigned dec_adr:7;       //decoder adress
  unsigned dec_state:1;     //decoder state
  unsigned wait:4;          //wait time befor send command 0-15s
  unsigned forwardRoute:1;  //if set, dec_adr points to route
  unsigned spare:3;
} MemoryElement;

struct MemoryRoute
{ unsigned fromKey:7;       //key starting route
  unsigned bidirectional:1; //route works in both direktions
  unsigned toKey:7;         //key end route
  unsigned targetDefined:1; //tbc
} MemoryRoute;

struct EEProm
{
  struct MemoryElement arrMemoryElements[MAX_MEMORY_ELEMENTS];
  struct MemoryRoute arrMemoryRoutes[MAX_MEMORY_ROUTES];
} EEProm;

//settings
unsigned char InitRoute = 1;
unsigned char InitRouteWait = 5; //[sec]
unsigned char InitWaitBetweenSwitch = 5; //[10ms]

//EEprom
struct EEProm EEPPromShadow EEMEM;
unsigned char EEPInitRoute EEMEM;
unsigned char EEPInitRouteWait EEMEM; //[sec]
unsigned char EEPInitWaitBetweenSwitch EEMEM; //[10ms]
unsigned char EEPGuilty EEMEM;

//******************************************************************************************
// global variables
//****************************************************************************************** 
char  UARTReceiveBuffer[100];
char  UARTLastCommand[100];
char* pLastReceiveByte = 0;
char  bReceivedCommandComplete;
char  cStatusMode = 'I';        //I = idle
char  cStatusError = 0;         //0 = no error

char cTimerBase = 19; //1160us Timer
long lLedTaskTimer = 0;
long lKeybTaskTimer = 0;
long lMemoryTaskTimer = 0;

unsigned char cKey[MAX_VIRTUAL_KEYS];

char RuningMemory = false;
char LastPressedKey = 0;
char FirstPressedKey = 0;
char SecondPressedKey = 0;
char keyActive = false;
uint8_t indexFIFOBuffer = 0xFF;
char toggleActive = true;

char HeartbeatActive = false;
char HeartbeatNackCount = 0;

#define LED_STATE_IDLE    0
#define LED_STATE_WAITING 1
#define LED_STATE_COMMIT  2
#define LED_STATE_NACK    3

unsigned char ledActiveState = LED_STATE_IDLE;

#define MEMORY_STATE_IDLE               0
#define MEMORY_STATE_FIRST_KEY_AKTIVE   1
#define MEMORY_STATE_WAITING_SECOND_KEY 2
#define MEMORY_STATE_FINISH_ROUTE       3
#define MEMORY_STATE_WAIT_AFTER         4
#define MEMORY_STATE_SWITCH_IT          5

unsigned char memoryActiveState = MEMORY_STATE_IDLE;
unsigned char memoryNextActiveState = MEMORY_STATE_IDLE;
unsigned long memoryTimeout = 0;
unsigned char memoryActualIndex = 0;

#define KEYB_STATE_IDLE               0
#define KEYB_STATE_SET_NEXT_GROUP     1
#define KEYB_STATE_READ_GROUP         2

unsigned char keybActiveState = KEYB_STATE_IDLE;
unsigned long keybTimeout = 0;
unsigned char keybActiveGroup = 0;
unsigned char keybActiveKey = 0;

//******************************************************************************************
// Init Ports
//******************************************************************************************
void InitPorts(void)
{
#ifdef __AVR_ATmega8__
  //init ports
  PORTB = 0x0; // external pullup
  PORTD = 0x0; // external pullup
  PORTC = 0x0; // external pullup
  DDRB = 0x0;
  DDRD = 0x0;
  DDRC = 0x0;

  PORTC = 1<<PC5;	/* turn the LED off */
  DDRC = 1<<PC5;	/* PC5 as output - the LED is there */

  //care amplifier outputs
  PORTB |= 1<<PB0;	/* Output A LOW  */
  DDRB |= 1<<PB0;	/* PB0 as output */
  PORTB |= 1<<PB1;	/* Output B LOW  */
  DDRB |= 1<<PB1;	/* PB1 as output */
#endif

#ifdef __AVR_ATmega32__
  //init ports
  PORTA = 0x0; // external pullup
  PORTB = 0x0; // external pullup
  PORTC = 0x0; // external pullup
  PORTD = 0x0; // external pullup
  DDRA = 0x0;
  DDRB = 0x0;
  DDRC = 0x0;
  DDRD = 0x0;

  //care LED port
  PORTB |= 1<<PB4;
  DDRB |= 1<<PB4;

  //care amplifier outputs
  PORTD |= 1<<PIN_OUT1;	/* Output A LOW  */
  DDRD |= 1<<PIN_OUT1;	/* driver enable 0 */
  PORTD |= 1<<PIN_OUT2;	/* Output B LOW  */
  DDRD |= 1<<PIN_OUT2;	/* driver enable 1 */
#endif

  //clear keys array
  memset(&cKey, 0, sizeof(cKey));

  //activate global interrupts
  sei();
}

//******************************************************************************************
// Init Timer
// 8bit Timer is main timer and support 1ms base timer
//******************************************************************************************
void InitTimer(void) 
{
  // Timer 0 konfigurieren
  TCCR0 = (1<<CS01); // Prescaler 8
  // Overflow Interrupt erlauben
  TIMSK |= (1<<TOIE0);
}

//******************************************************************************************
// Overflow Interrupt Handler
// called if TCNT0 changes 255 to 0 (256 Steps),
// freq_nopreload = 8000000 / 8 / 256 = 3906.25 Hz, ^= 256us
// freq_preload60 = 5000.18 Hz ^= 200us
// freq_preload202 ^= 58 us
// freq_preload144 ^= 116 us
//******************************************************************************************
ISR (TIMER0_OVF_vect)
{ //preload
  TCNT0 = 60;
  //care base timer
  if (cTimerBase>0) {
    cTimerBase--;
  } else {
    cTimerBase = 4;
    //care other timers, decrement if set
    if (lLedTaskTimer > 0) lLedTaskTimer--;
    if (lKeybTaskTimer > 0) lKeybTaskTimer--;
    if (lMemoryTaskTimer > 0) lMemoryTaskTimer--;
  }
}

//******************************************************************************************
// Simple LED Support
//	state = 0 -> Led Off
//	state = 1 -> Led On
// 	state !=[0,1] -> Led Toggle
//******************************************************************************************
void HeartbeatSet(unsigned char state)
{
#ifdef __AVR_ATmega8__
  switch (state)
  {
  case 0:
    PORTC &= ~(1<<5);
    break;
  case 1:
    PORTC |= 1<<5;
    break;
  default:
    if (PORTC & 1<<5)
      PORTC &= ~(1<<5);
    else
      PORTC |= 1<<5;
  }
#endif

#ifdef __AVR_ATmega32__
  switch (state)
  {
  case 0:
    PORTB &= ~(1<<PB4);
    break;
  case 1:
    PORTB |= 1<<PB4;
    break;
  default:
    if (PORTB & 1<<PB4)
      PORTB &= ~(1<<PB4);
    else
      PORTB |= 1<<PB4;
  }
#endif
}

//******************************************************************************************
// DCC Burst Functions
//******************************************************************************************
void DCCSet(void)
{ //set amp port
#ifdef __AVR_ATmega8__
  PORTB &= ~(1<<0);
  PORTB |=  (1<<1);
#endif
#ifdef __AVR_ATmega32__
  PORTD &= ~(1<<PIN_OUT1);
  PORTD |=  1<<PIN_OUT2;
#endif
}

void DCCDelete(void)
{ //delete amp port
#ifdef __AVR_ATmega8__
  PORTB |=  (1<<0);
  PORTB &= ~(1<<1);
#endif
#ifdef __AVR_ATmega32__
  PORTD &= ~(1<<PIN_OUT2);
  PORTD |=  1<<PIN_OUT1;
#endif
}

void DCCBitOne(void)
{
  DCCSet();
  //wait 58us
  delay_us(56);
  //delete ports
  DCCDelete();
  //wait 58us
  delay_us(51);
}

void DCCBitZero(void)
{
  DCCSet();
  //wait 58us
  delay_us(114);
  //delete ports
  DCCDelete();
  //wait 58us
  delay_us(105);

}

void DCCBitZeroLong(void)
{
  DCCSet();
  delay_ms(2);
  DCCDelete();
  delay_ms(2);
}

void DCCSync(void)
{ char i;
  //more than 10 ones
  for (i=0;i<16;i++)
  {
    DCCBitOne();
  }
}

void DCCStartbit(void)
{ //start bit
  DCCBitZero();
}

void DCCByte(char cByte)
{ char i;
  for (i=7;i>=0;i--)
  { //shift and compare
    if (cByte & 1<<i) {
      DCCBitOne();
    } else {
      DCCBitZero();
    }
  }
}

void DCCStopbit(void)
{ //start bit
  DCCBitOne();
}

void DCCToggle(void)
{ static char dcctoggleflag = 0;
  //check flag
  if (dcctoggleflag) {
    //delete ports
    DCCDelete();
  } else {
    //set ports
    DCCSet();
  }
  //invert
  dcctoggleflag = !dcctoggleflag;
}

char DCCSwitch(unsigned char p_cDecAdresse, unsigned char p_cDecOutput, unsigned char p_cState)
{ 
  unsigned char adressbyte;
  unsigned char databyte;
  unsigned char checksumbyte;

  //Nr. 0 modules not used
  p_cDecAdresse++;

  //check ranges
  if ((p_cDecOutput > 3) || (p_cState > 1))
  { //leave
    return false;
  }

  // DCC basic accessory decoder format 
  // 10AAAAAA 0 1AAADAAC 0
  // the middle adress block needs to be inverted (results in the xor below)
  // D=1 means coil on, D=0 coil off
  // the last two adress bits are usually known as decoder output 1-4
  // C refers the coil to be activated (usually straight/round or green/red)
  adressbyte = 0x80 + (p_cDecAdresse & 0x3F);
  databyte  = 0x80 + ((p_cDecAdresse / 0x40) ^ 0x07) * 0x10;
  databyte  += ((p_cDecOutput & 0x03) << 1);
  databyte  += (p_cState & 0x01);
  databyte  += 0x08;
  checksumbyte  = adressbyte ^ databyte;

  // Overflow Interrupt erlauben
  TIMSK &= ~(1<<TOIE0);

  //send a signal
  DCCBitZeroLong();    //oszi
  DCCSync();           //synchronisation
  DCCStartbit();
  DCCByte(adressbyte); //adress
  DCCStartbit();
  DCCByte(databyte);  //data
  DCCStartbit();
  DCCByte(checksumbyte); //prüfsumme
  DCCStopbit();
  DCCBitZeroLong();    //oszi

  // Overflow Interrupt erlauben
  TIMSK |= (1<<TOIE0);
  
  //tell user
  printf_P
    ( PSTR("DW;%u;%u;%u(MA=%u)\n\r")
    , p_cDecAdresse
    , p_cDecOutput
    , p_cState
    , ((p_cDecAdresse-1) * 4) + p_cDecOutput +1
    );

  return true;
}

//******************************************************************************************
// FIFO functions (www.mikrocontroller.net/articles/FIFO)
//******************************************************************************************

#define BUFFER_SIZE 64 // muss 2^n betragen (8, 16, 32, 64 ...)
#define BUFFER_MASK (BUFFER_SIZE-1) // Klammern auf keinen Fall vergessen

struct FIFOBuffer 
{
  uint8_t data[BUFFER_SIZE];
  uint8_t read; // zeigt auf das Feld mit dem ältesten Inhalt
  uint8_t write; // zeigt immer auf leeres Feld
} FIFObuffer = {{}, 0, 0};

uint8_t FIFOBufferIn(uint8_t byte)
{
  uint8_t next = ((FIFObuffer.write + 1) & BUFFER_MASK);
  if (FIFObuffer.read == next)
    return false;
  //FIFObuffer.data[FIFObuffer.write] = byte; //schneller
  FIFObuffer.data[FIFObuffer.write & BUFFER_MASK] = byte; // absolut Sicher
  FIFObuffer.write = next;
  return true;
}

uint8_t FIFOBufferOut(uint8_t *pByte)
{
  if (FIFObuffer.read == FIFObuffer.write)
    return false;
  *pByte = FIFObuffer.data[FIFObuffer.read];
  FIFObuffer.read = (FIFObuffer.read+1) & BUFFER_MASK;
  return true;
}

//******************************************************************************************
// Selftest Support
//******************************************************************************************
void Selftest(void)
{ 
  #ifdef __AVR_ATmega32__
    //just tell i am alive by blinking three times
    HeartbeatSet(0);
    delay_ms(200);
    HeartbeatSet(1);
    delay_ms(200);
    HeartbeatSet(0);
    delay_ms(200);
    HeartbeatSet(1);
    delay_ms(200);
    HeartbeatSet(0);
    delay_ms(200);
    HeartbeatSet(1);
    delay_ms(200);
  #endif
}

#define nop() asm volatile("nop")

//very simple delay
//based on: for (i=10000;i;i--); //ca. 181ms
void delay_ms(unsigned int uiDuration) 
{
  unsigned int i;
  unsigned int j;
  for (j=uiDuration;j;j--) {
    for (i=796;i;i--) nop(); //loops nearly 1ms at 8Mhz Crystal
  }
}

void delay_us(unsigned int uiDuration) 
{
  unsigned int i;
  for (i=uiDuration;i;i--) nop(); //loops nearly 58us at 8Mhz Crystal
}

//******************************************************************************************
// UART functions
//******************************************************************************************
// Init UART to 8 bit, no control (!), 1 stop
void UARTInit(void)
{ //set calculated baudrate (defines)
  UBRRH = UBRR_VAL >> 8;
  UBRRL = UBRR_VAL & 0xFF;
  //Enable Receiver and Transmitter
  UCSRB = (1<<RXEN)|(1<<TXEN);
  //Set frame format: 8data, 1stop bit
  UCSRC = (1<<URSEL)|(1<<UCSZ1)|(1<<UCSZ0);
  // target UARTs to Stdout
  stdout = &uart_stream;
  //clear flag
  bReceivedCommandComplete = false;
  //reset pointer
  pLastReceiveByte = UARTReceiveBuffer;
}
 
// output function for printf
int uart_putchar( char c, FILE *stream )
{
  // wait for empty buffer
  while ( !( UCSRA & (1<<UDRE)) );
  // send char
  UDR = c;
  return 0;
}

// Get a char from UART or return zero
char UARTReceive(void)
{
  if (UCSRA & (1<<RXC))
    return UDR;
  else    /* no data pending */
    return 0;
}

/* Zeichen empfangen */
char UARTGetC(void)
{
    while (!(UCSRA & (1<<RXC)))   // warten bis Zeichen verfuegbar
        ;
    return UDR;                   // Zeichen aus UDR an Aufrufer zurueckgeben
}

void UARTTransmit(char data)
{
  while (!( UCSRA & (1<<UDRE)) );
  /* Put data into buffer, sends the data */
  UDR = data;
}

void UARTSendString(const char * pStr)
{ //send till zero
  while (*pStr) {
    UARTTransmit(*pStr);
    pStr++;
    delay_ms(1);
  }

}

void UARTHello(void)
{
  //hello world
  #ifdef __AVR_ATmega32__
    printf_P(PSTR("\x1B[2J\x1B[Hdcc_gen v%u.%u ATMega%u\n\r" ), VERSION, SUBVERSION, MEGA_CPU);
    printf_P(PSTR("type '?' for help...\n\r"));
  #endif
}

void CopyNumericToken
  ( char * dest
  , char * src
  , char length
  )
{ //temps
  unsigned char cCount = 0;
  //check param
  if (dest && src) {
    //copy nums
    while ((*src >= 48) && (*src <= 57) && (cCount<length)) 
    { //copy
      *dest = *src;
      //next
      dest++;
      src++;
      cCount++;
      //close string
      *dest = 0;
    }
  }
}

char GetTokenToChar
  ( char * pcBuffer
  , char cIndex
  )
{ //temps
  char cRet = 0;
  char bFound = false;
  char cCount = 0;
  char cSeperator = ';';
  char * pcTemp = pcBuffer;
  char strNumBuffer[10];
  unsigned char countNumBuffer = 0;
  //check parameter
  if (!pcBuffer) return cRet;
  //loop buffer
  while (!bFound) {
    //check for separator
    if ((*pcTemp == cSeperator)||(*pcTemp == '\r')||(*pcTemp == '\n')||(*pcTemp == 0)) {
      //got one
      cCount++;
      //check index
      if (cCount == cIndex) {
        //calc length of token
        countNumBuffer = pcTemp-pcBuffer;
        //check length
        if (countNumBuffer < 10) {
          //copy string
          CopyNumericToken(strNumBuffer, pcBuffer, countNumBuffer);
          //convert to number
          cRet = atoi(strNumBuffer);
        }
        //leave
        bFound = true;
      } else { 
        //set next starting point
        pcBuffer = pcTemp+1;
      }
    }
    if ((*pcTemp == '\n')||(*pcTemp == '\r')||(*pcTemp == 0))
    { //leave anyway
      bFound = true;
    } else {
      //next sign
      pcTemp++;
    }
  }
  //fin
  return cRet;
}
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
int main(void)
{ //init all hardware stuff
  InitPorts();
  UARTInit();
  Selftest();
  UARTHello();
  InitTimer();
  MemoryInit();
  //send promt
  UARTSendString("> ");
  //wait forever for receive
  while (1)
  { //timer0
    LEDTask();
    //timer1
    KeybTask();
    //timer2
    MemoryTask();
    //care keyboard
    KeybRead();
    //care comunication
    UARTComunicate();
  }
  //fin
  return 0;
}

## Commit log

2020-04-17 add workspace, add fuses
2020-04-17 fix string usage for small cpus, fix warnings
    [main.c]
2022-04-28 Get it running again in Platform.io, fix DCC switch command (works now with SandEi, digital-bahn.de). Kown issue in UART: does not answer correctly
    [main.c]
2022-05-02 refactor state machine, fix memory and UART
    [main.c]
2023-12-21 add parameter to switch off idle toggle, add toggle for switches, fix delays, optimize flash
    [main.c]
2023-12-21 fix merge, checked with Arduino DCC decoder
    [main.c]
2023-12-23 add hardware
    [DCCGen_ATMEGA_V2_Haka.brd, DCCGen_ATMEGA_V2_Haka.sch, DCCGen_ATMEGA_V2_Haka_Rev1.brd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]
2023-12-23 add config for ATMega32, checked with v5 board
